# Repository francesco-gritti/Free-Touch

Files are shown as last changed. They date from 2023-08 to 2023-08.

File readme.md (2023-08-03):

# Free Touch

Water dispenser build for demonstration purpose without the device installed

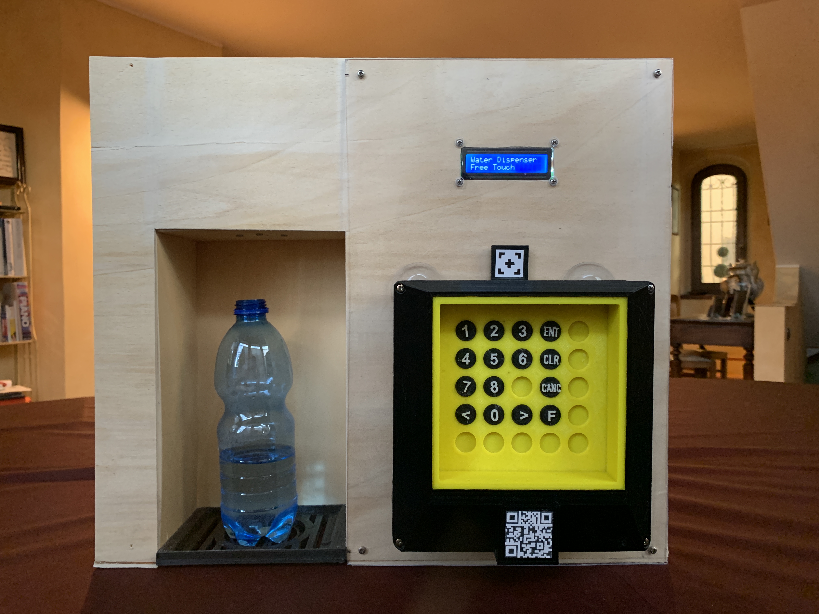
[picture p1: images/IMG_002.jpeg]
Water dispenser with the device installed


Free touch (which was tought during Covid 19) is a simple device that can be adapted to any keypad layout (like the ones of water dispenser machines, elevators and so on) and once mounted on top of it can press the buttons for you, avoiding you to have to touch anything. You can tell it the will to press a button by putting your finger closer to the target or by connecting with the smartphone via bluetooth

Free Touch can be adapted to the desired keypad layout just by taking a picture of it: an algorithm will recognize the buttons and calculate their position. Free Touch is then equipped with a tip that can move into the space and physically press buttons for you

Of course it would be easier to design products (water dispenser machines, elevators, ...) already equipped with bluetooth connectivity or non-touch user interaction, however there are so many machines that rely upon contact already that it would require an enormous effort to modifying them all

Okay this was me trying to make it look useful. It's not but conversely I think it's a nice little concentrate of engigneering: both electronics, mechanics and Informatics
Is that kind of device that solves a very simple problem in a very complicated way: wouldn't it be easier to design sime kind of stick you can hold in your hand and press the buttons with?
I still think that it was worth designing, building and programming it because it allowed me to enhance my knoledge of computer vision, 3d printing, mechanical design and embedded programming and was so much fun!

## Mobile App
For configuring the device (the process is explained in the next section) and for using it, I developed an application for smartphones using the Flutter framework so that it can be compiled for IOS and Android natively. The first version of the app used filtering, contrast enhancing and contour detection algorithm developed by me. In the second version I rightfully decided to integrate OpenCV which, of course, made the development much easier. Yet I think is a good way of proceeding: first develope something that work (doesn't have to be perfect) from scratch, then start using a library or a framework: first you learn from the ground up how something work and second but most important you can really appreciate those people that spend theire lives developing and then distributing theire work as open source. Many thanks to them!

Okay back to where I left...

## Configuration 
Before I mentioned that the device could be configured by taking a picture of it and can be controlled through bluetooth
Usually the configuration process confure people so I will try to explain how it works here:
- first of all you have to put a tag above the keypad you whish to configure (it will act as a reference to the algorithm to determine position and sizes)

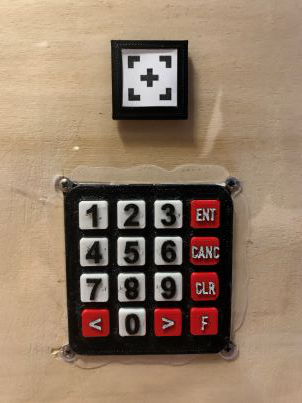
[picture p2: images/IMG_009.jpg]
Keyboard and tag

- than you open the application and connect to the device by scanning it's QR code

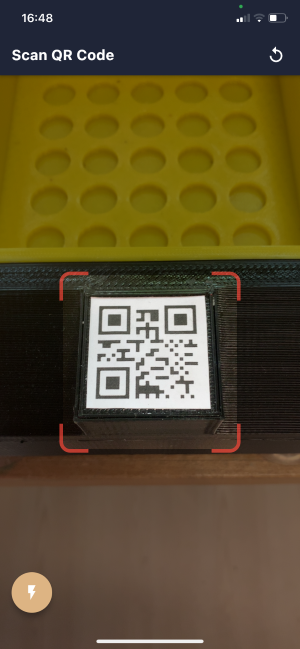
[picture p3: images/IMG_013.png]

- you take a picture of the keypad icluding the tag and the algorithm will automatically detect close edges that resembles pushbuttons



- Select the buttons you whish to configure

- Install the device aligning the slot on the top with the tag (this is necessary since the tag is the reference of the whole system and its position must be known)

Well Done! you can now press buttons at a distance, like magic!

this is the screen that appears when you connect to the device

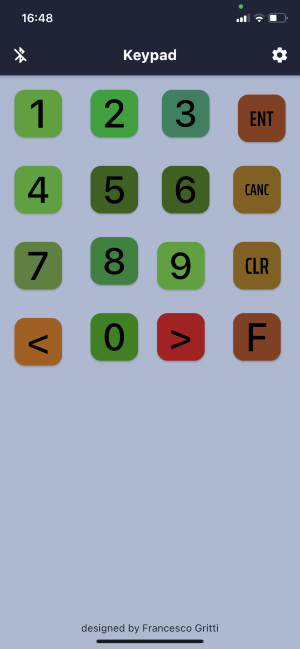
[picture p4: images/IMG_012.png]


## IR Sensor
on the front of the device there is a configurable matrix IR sensor matrix that allow the user to press the button by putting it's finger closer to it

The matrix is configurable in the meaning that behind each cell scanned by the IR sensors there is a slot where you can put an insert with written the actual button it corresponds to. This way the user can interact with it in a very natural way

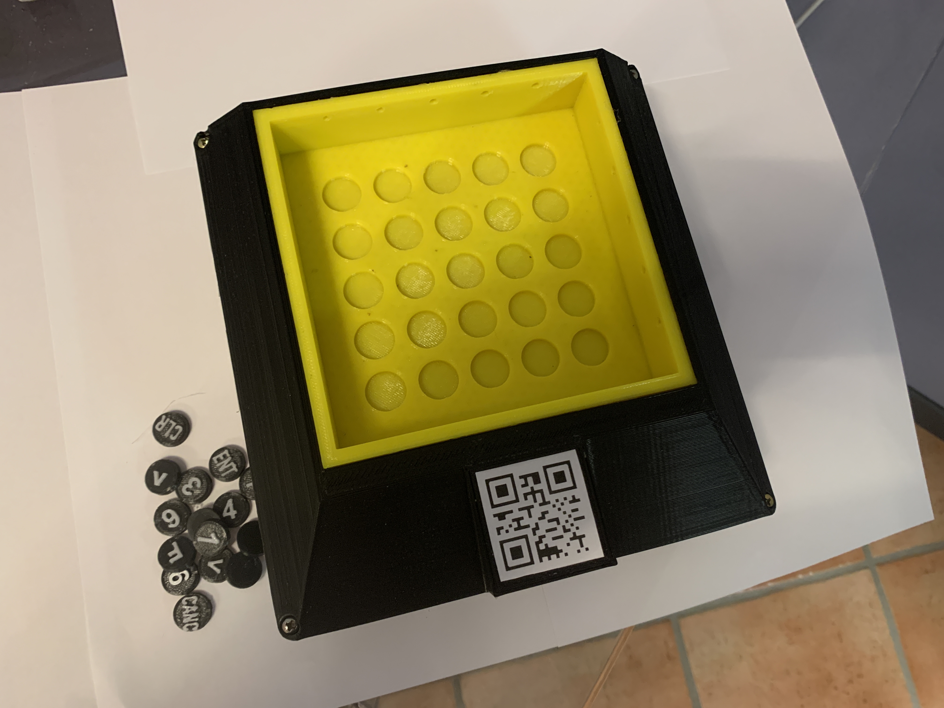
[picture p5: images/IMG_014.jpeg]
Before configuration


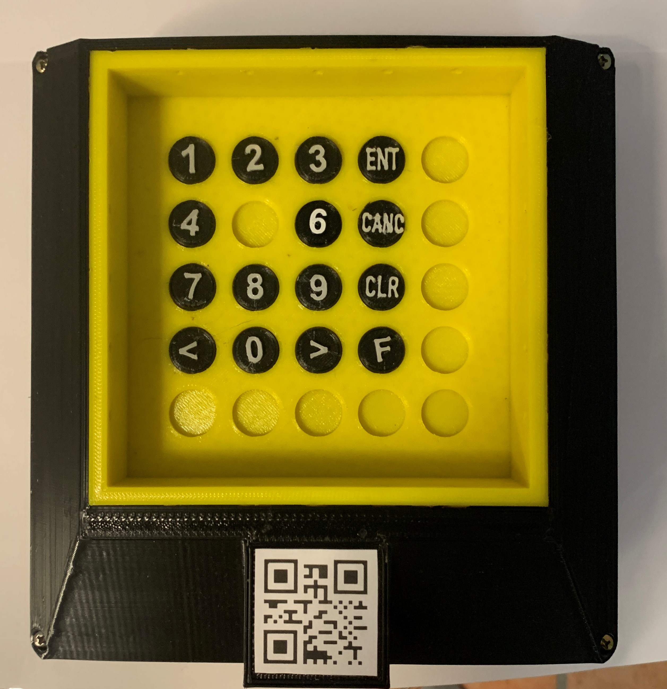
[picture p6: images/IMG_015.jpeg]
After configuration


## Mechanics

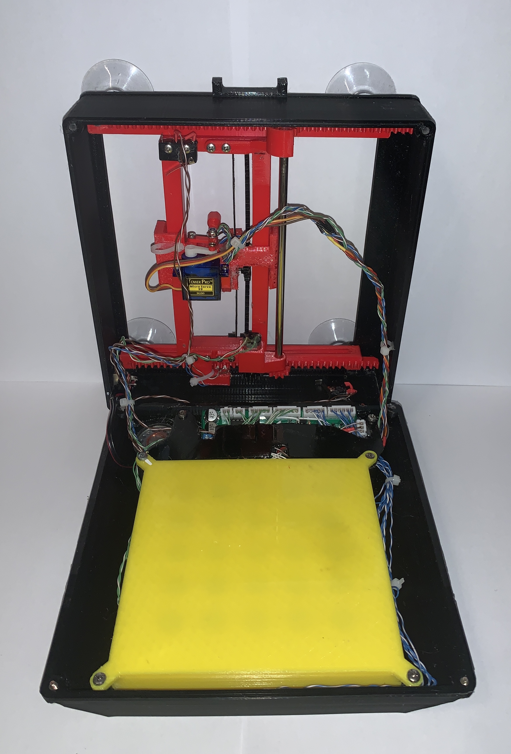
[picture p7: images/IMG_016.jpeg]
Internal of the device


All the mechanical parts are 3d printed using PETG. I decided to use this material since there are parts that slide on each other and PETG felt like a better material for this purpose in terms of friction with respect to PLA or ABS, and I didn't want to use PLA since it can easily deform even at not so high temperatures

I used little DC motors with reduction which turned out to be perfect for this application: small, light way yet they have good torque and speed

The axis position is monitored by optical encoder that were 3D printed int the structure itself

the buttons are effectively pressed by a sg90 servo motor

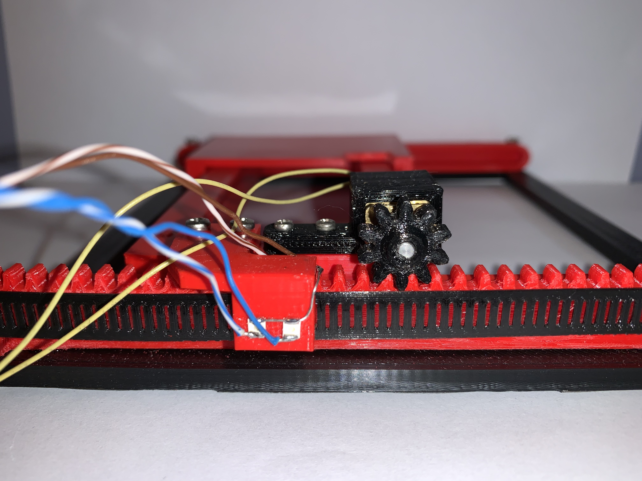
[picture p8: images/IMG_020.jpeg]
Details of the embedded encoder of one of the axis


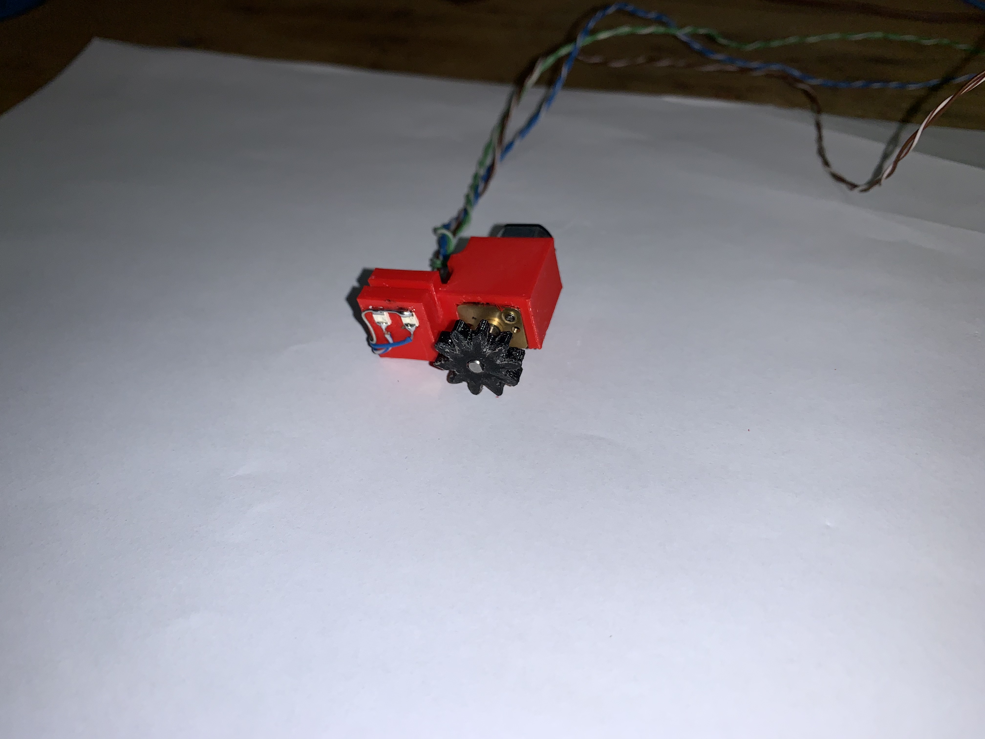
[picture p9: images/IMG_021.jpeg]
Details of oen of the motor assembly with embedded IR emitter and receiver to read position


## Electronics
And now the time for electronics

### Microcontroller
As for the microcontroller I have used the PIC16LF18456 which has a generous amount of peripherals, RAM and program memory, more than enough for this project

### Analog IR Signal Conditioning
IR sensor are driven at 1kHz so that the slow varying influence of light of the environment can be filtered out with active filters. no one wants a button to be pressed just because a cloud covered the sun for frew seconds!

### Bluetooth
The bluetooth connectivity is handled through Microchip's module ... communicating with the microcontroller via AT commands over UART

### PCB
I was a bit in a rush (as every time when you have a deadline to the project) and when designing the PCB I made some mistakes (that is why there should be always a version 2.0 of a PCB) but luckily that happens so frequently that even if it was two years ago I was already quite good at PCB rework
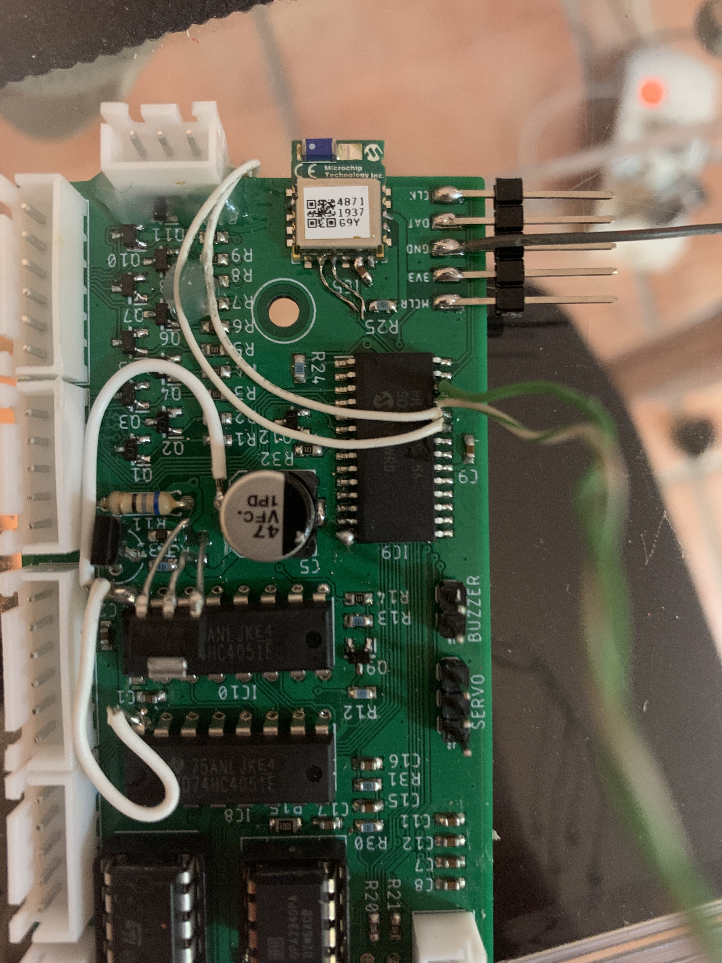
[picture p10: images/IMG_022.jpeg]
Issues here and there with the PCB design


## Cable management
I was almost forgetting (as I did while designing the device): cable management
In fact it's simple to overlook during design at cable management but it is most of the times critical. In this project everything had to fit in a tiny space and the axis had to move freely for almost the entire widtrh and length of the device. If even a tiny cable got stucked somewhere in the internal structure, the tip was blocked and many bad things can happen
Luckily after some trial and errors I managed to fix the cable in a very lovely way that was nicely organized and allowed the axis to move smoothly

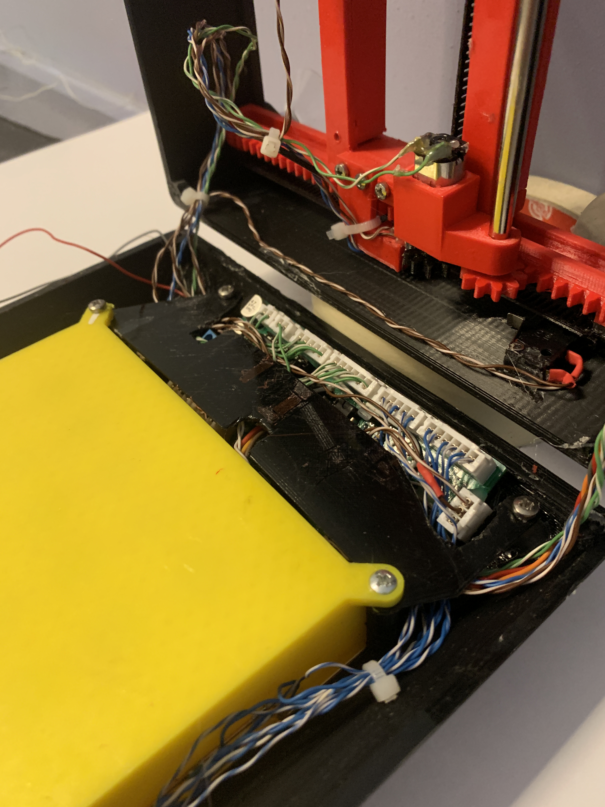
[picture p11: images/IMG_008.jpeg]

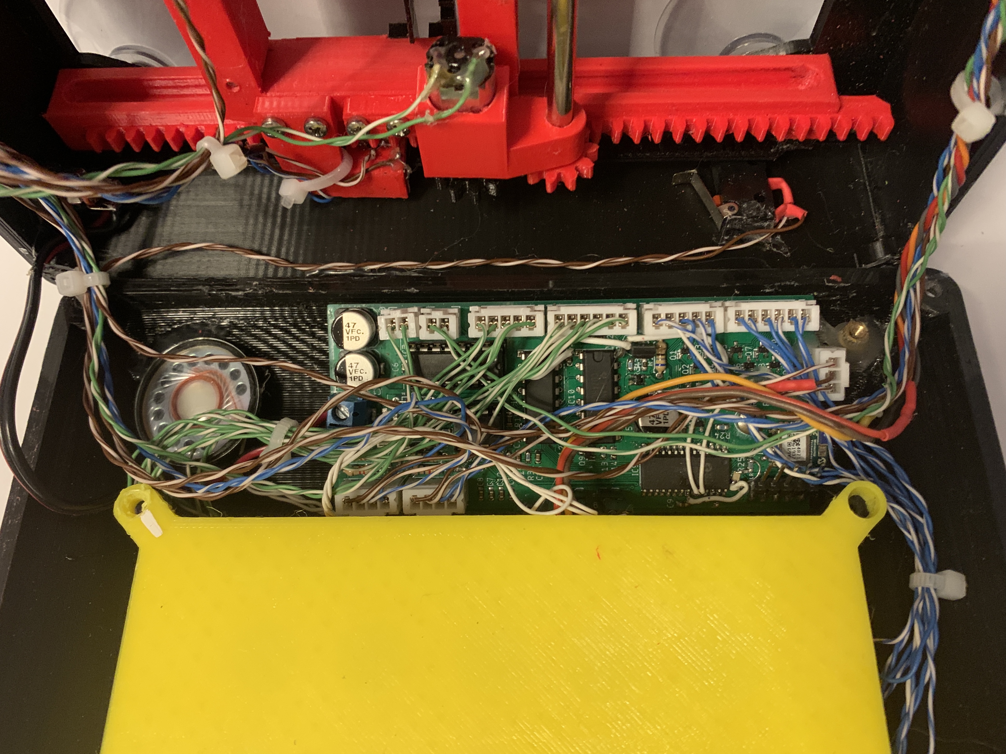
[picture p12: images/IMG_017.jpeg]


## Version 1.0

Well all I have been talking about and showing so far was version 2.0 of the device. Of course there have been a version 1.0 that was so ugly it almost feels a modern art creation
The concept is exactly the same, just messier. I will attach some pictures of it here 

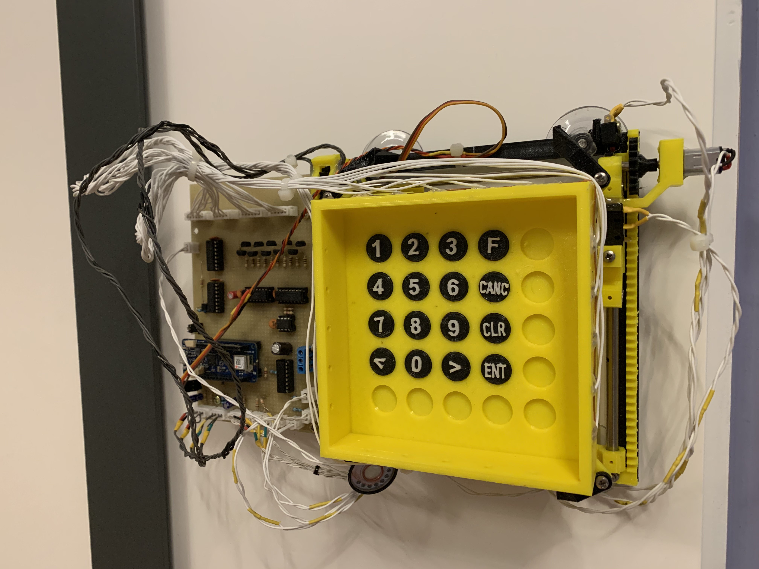
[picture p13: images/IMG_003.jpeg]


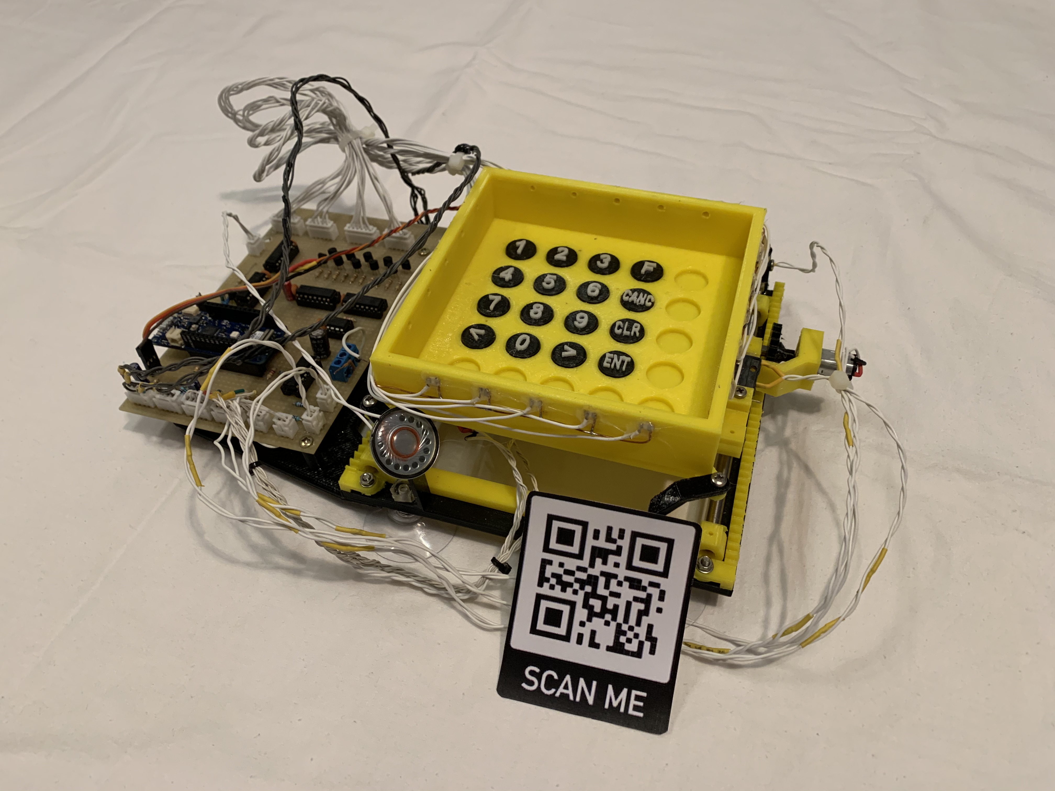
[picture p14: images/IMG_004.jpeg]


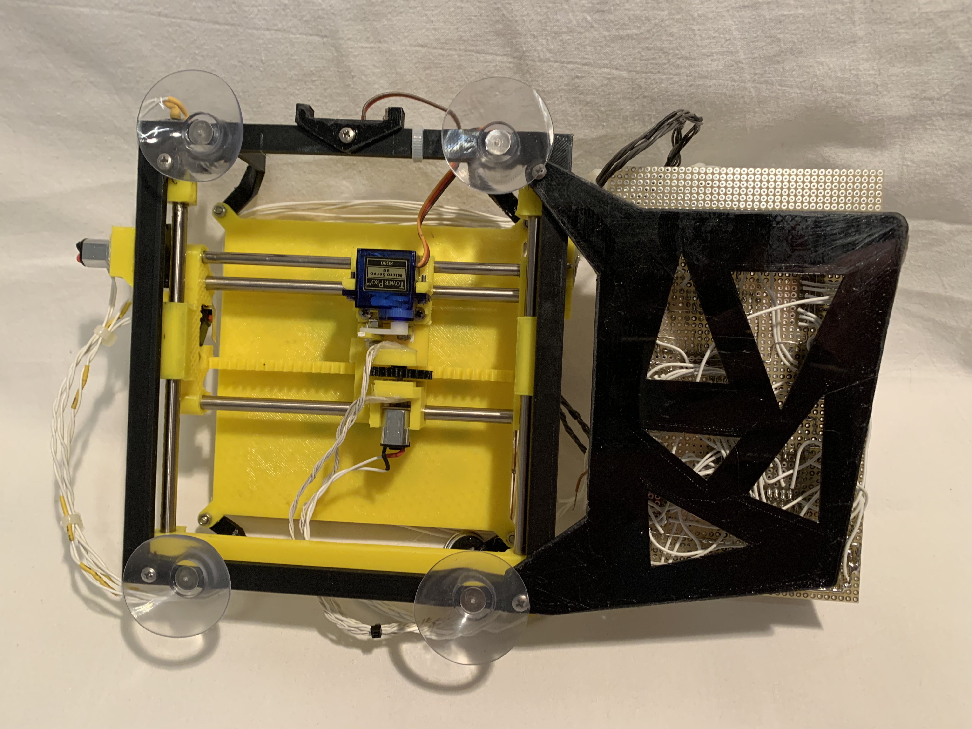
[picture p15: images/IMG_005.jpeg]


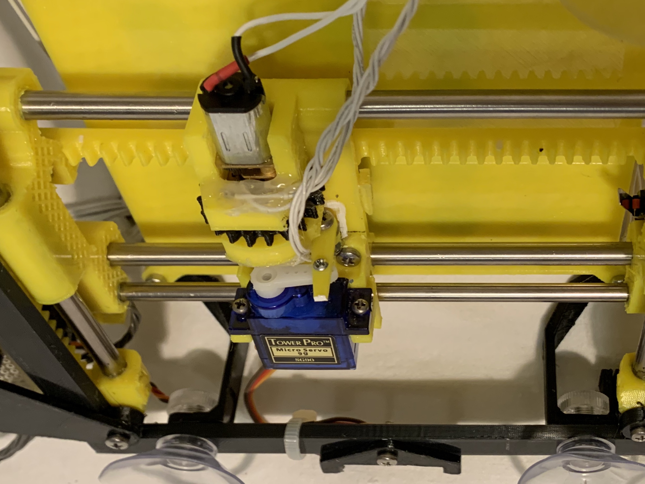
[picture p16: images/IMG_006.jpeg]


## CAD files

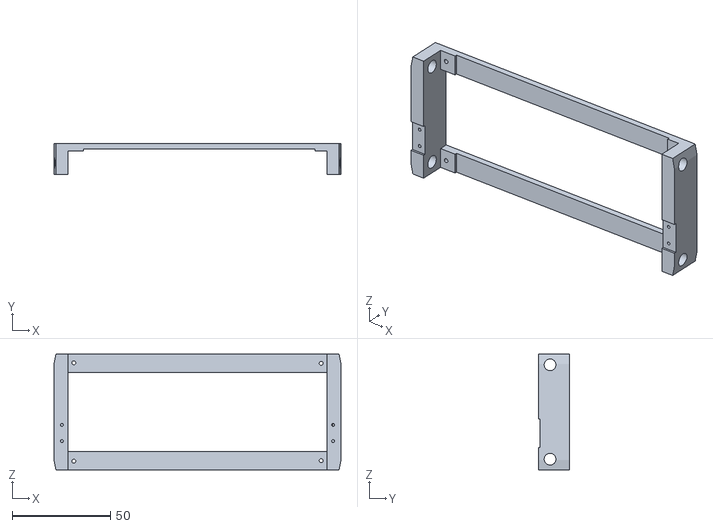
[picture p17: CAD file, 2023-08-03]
CAD/STL/Asse X/main_frame.stl
146.0 x 16.0 x 59.0

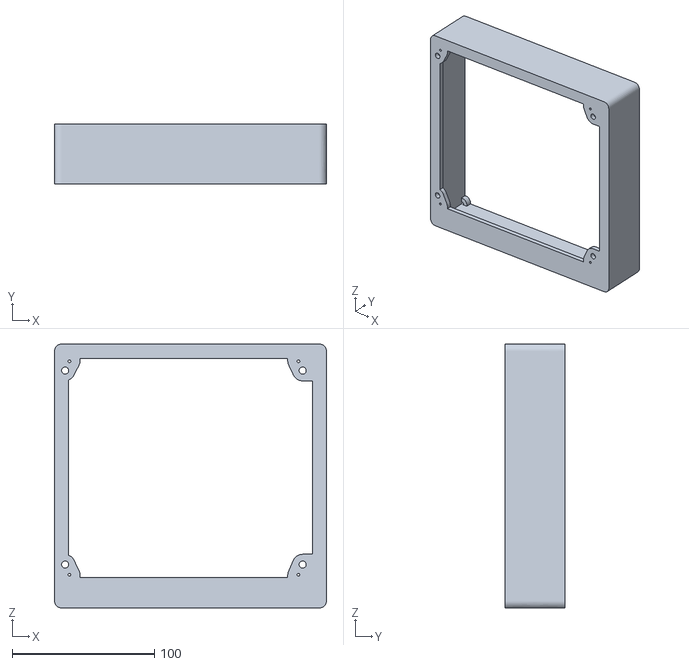
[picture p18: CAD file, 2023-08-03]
CAD/STL/keypad/enclosure_full.stl
191.2 x 42.0 x 185.5

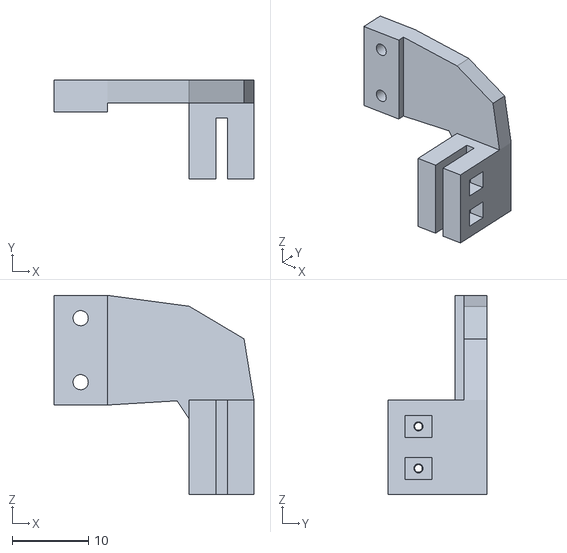
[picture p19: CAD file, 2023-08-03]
CAD/STL/Asse Y/enc_support.stl
26.2 x 13.0 x 26.2

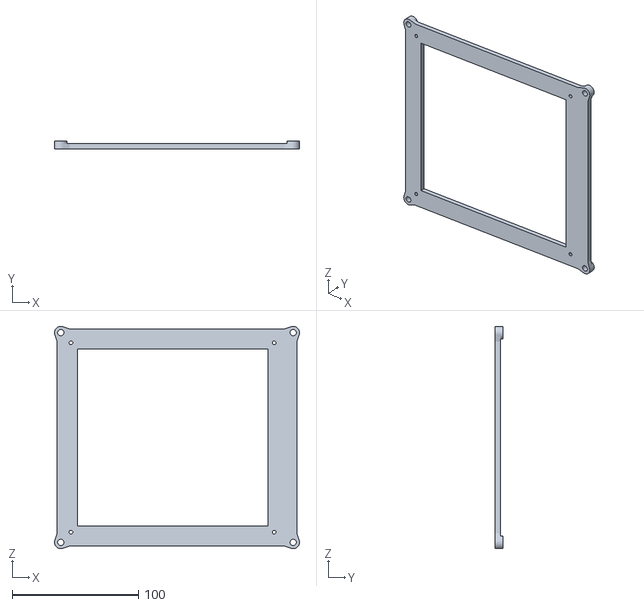
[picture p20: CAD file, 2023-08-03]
CAD/STL/base/base.stl
194.1 x 6.00 x 176.1

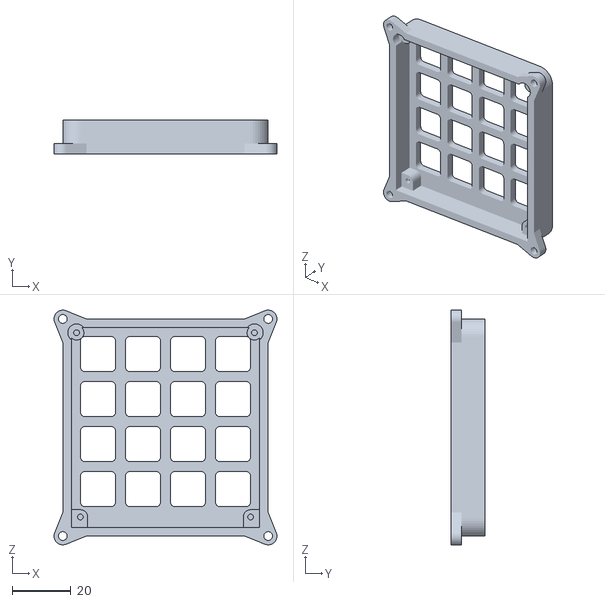
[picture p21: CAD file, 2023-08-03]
CAD/STL/keypad/keypad.stl
76.0 x 11.7 x 80.0

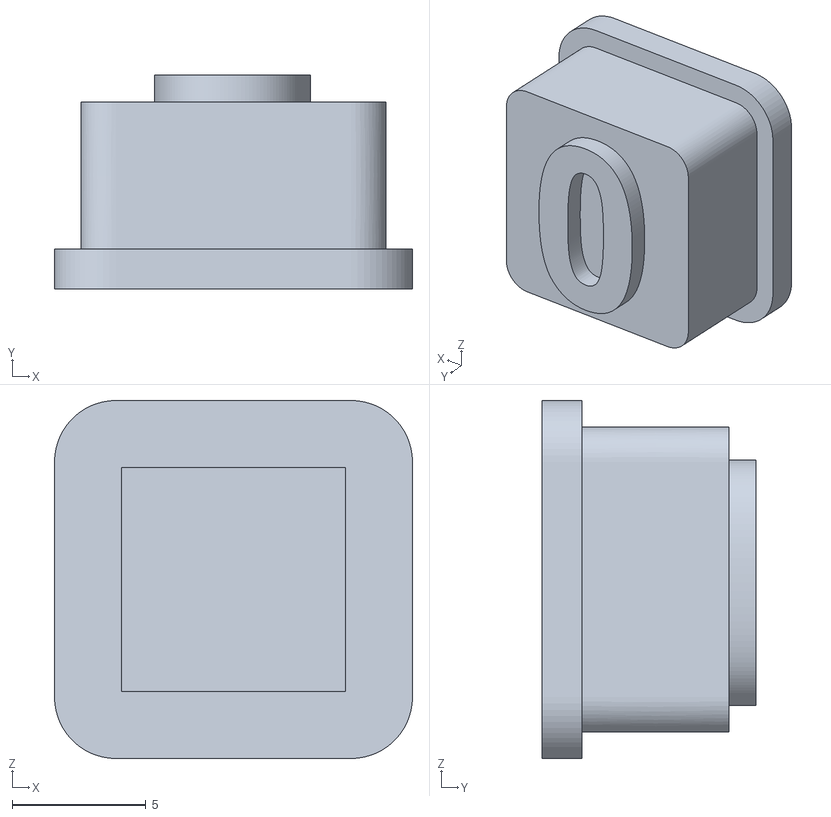
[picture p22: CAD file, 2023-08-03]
CAD/STL/keypad/keys/key0.stl
13.4 x 8.00 x 13.4

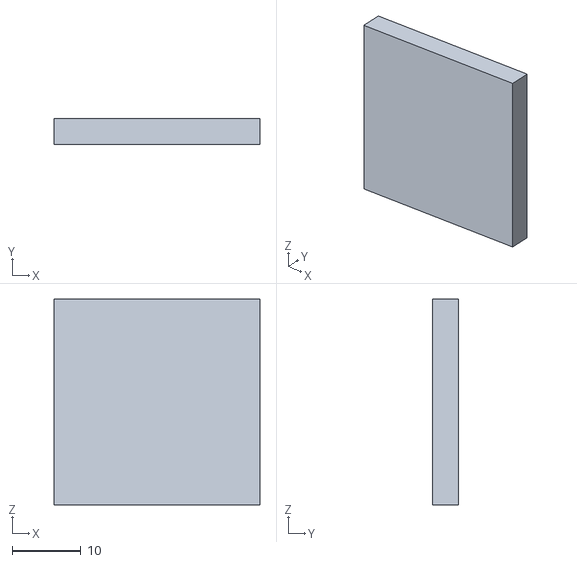
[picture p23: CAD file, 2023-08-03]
CAD/STL/tag_holder.stl
30.0 x 3.75 x 30.0

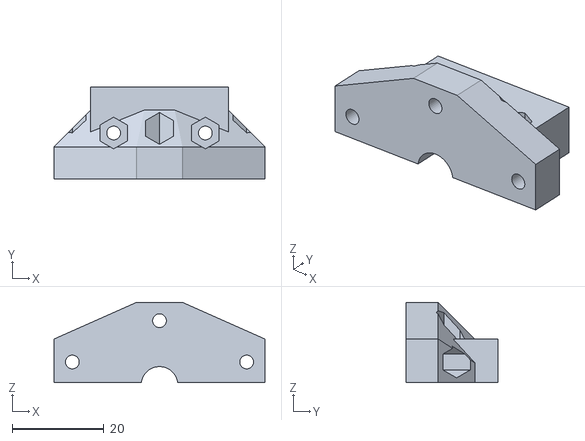
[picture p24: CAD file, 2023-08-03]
water dispenser/STL/Corpo1.stl
46.0 x 20.0 x 17.5

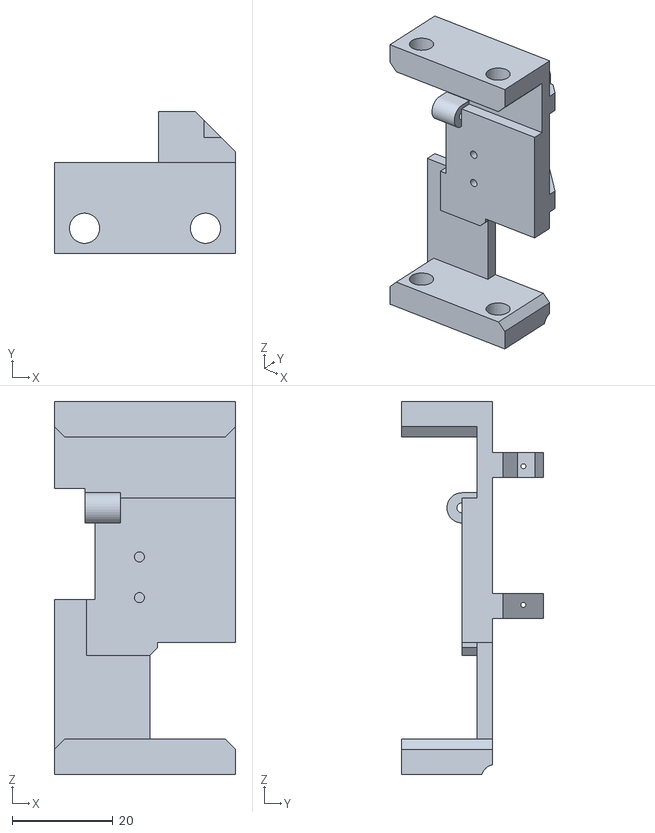
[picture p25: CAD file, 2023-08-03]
CAD/STL/Asse X/platform.stl
36.0 x 28.2 x 74.0

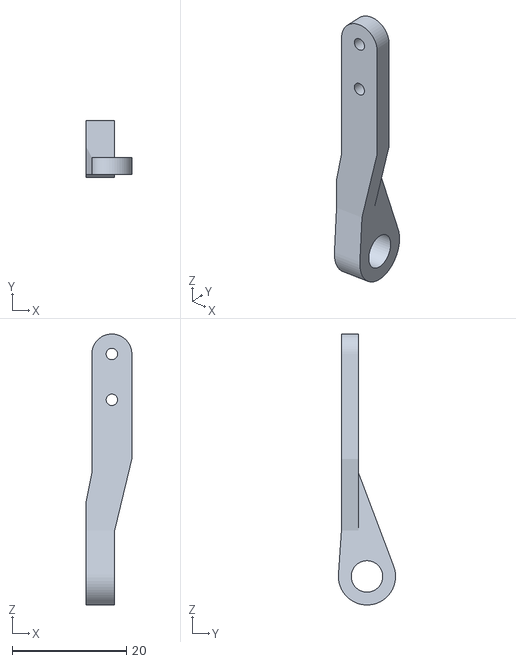
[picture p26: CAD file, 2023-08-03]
CAD/STL/Asse Y/supp1.stl
8.00 x 9.99 x 47.4

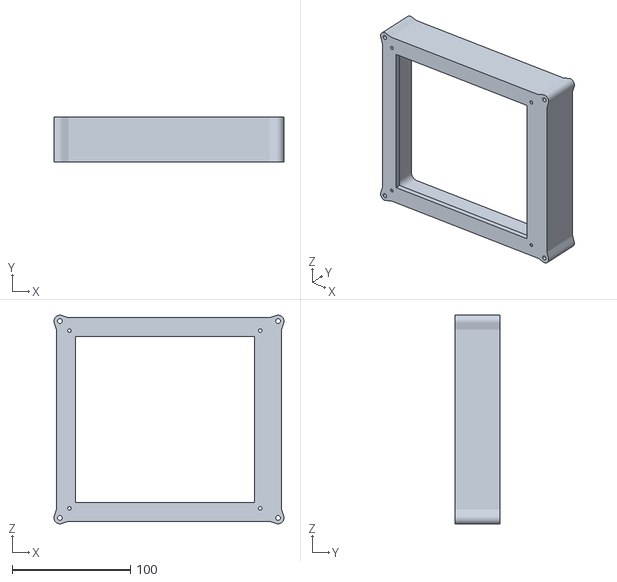
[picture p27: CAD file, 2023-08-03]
CAD/STL/base/enclosure.stl
194.1 x 38.0 x 176.1

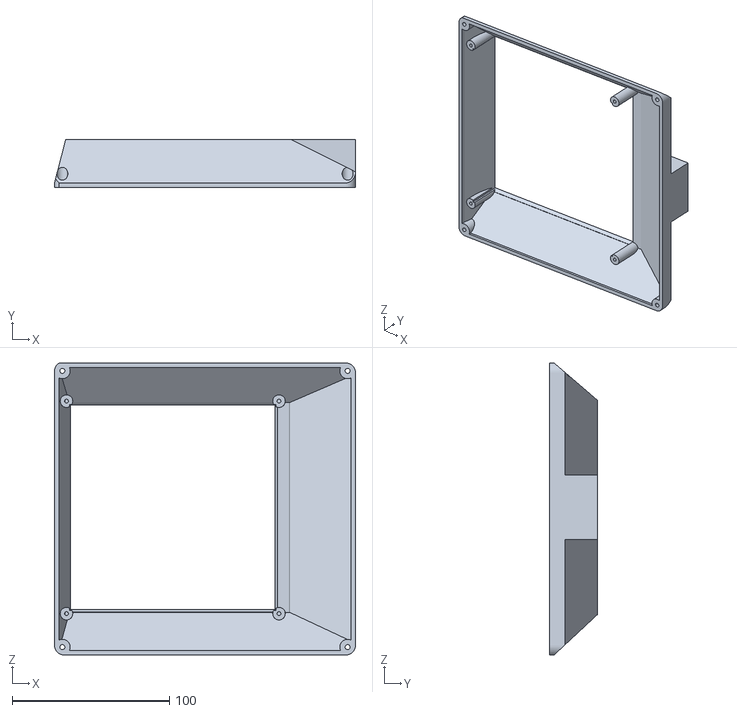
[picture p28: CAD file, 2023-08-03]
CAD/STL/keypad/enclosure_top.stl
191.2 x 30.6 x 185.5

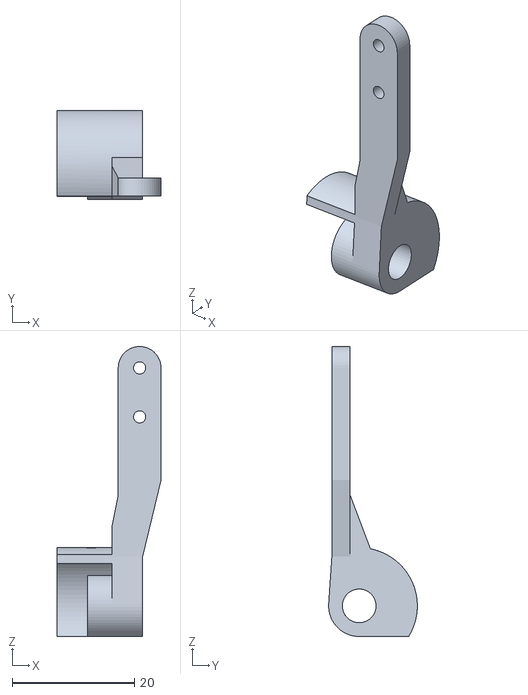
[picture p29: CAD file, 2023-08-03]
CAD/STL/s1.stl
17.0 x 14.5 x 47.4

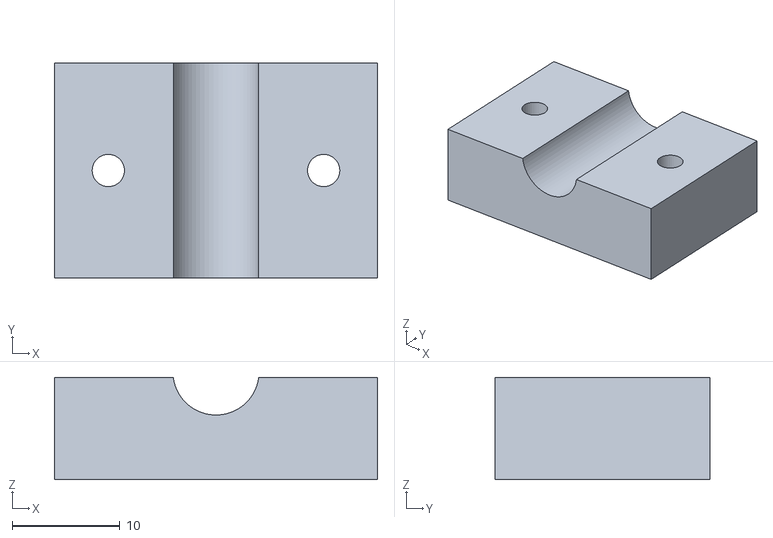
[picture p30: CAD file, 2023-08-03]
water dispenser/STL/Corpo2.stl
30.0 x 20.0 x 9.50

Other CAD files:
CAD/STL/keypad/keys/key5.stl
CAD/STL/Asse X/encoder_grid.stl
CAD/STL/Asse Y/guida.stl
CAD/STL/cable_squisher.stl
CAD/STL/Asse X/guide.stl
CAD/STL/Asse X/motor_encoder_support.stl
CAD/STL/Asse X/pin1.stl
CAD/STL/Asse X/rack.stl
CAD/STL/Asse X/tip1.stl
CAD/STL/Asse Y/Corpo1.stl
CAD/STL/Asse Y/encoder.stl
CAD/STL/Asse Y/gear.stl
CAD/STL/Asse Y/supp2.stl
CAD/STL/key_6.stl
CAD/STL/keypad/bottle_holder.stl
CAD/STL/keypad/key.stl
CAD/STL/keypad/keys/key1.stl
CAD/STL/keypad/keys/key2.stl
CAD/STL/keypad/keys/key3.stl
CAD/STL/keypad/keys/key4.stl
CAD/STL/keypad/keys/key6.stl
CAD/STL/keypad/keys/key7.stl
CAD/STL/keypad/keys/key8.stl
CAD/STL/keypad/keys/key9.stl
CAD/STL/keypad/keys/key_CANC.stl
CAD/STL/keypad/keys/key_CLR.stl
CAD/STL/keypad/keys/key_ENT.stl
CAD/STL/keypad/keys/key_F.stl
CAD/STL/keypad/keys/key.stl
CAD/STL/keypad/keys/key.stl
water dispenser/STL/pump_holder.stl

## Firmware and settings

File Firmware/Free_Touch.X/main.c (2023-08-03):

#include "main.h"



//#define DEBUG

// unique ID identifier of the device
const uint8_t manufacturerData[16] = "1234567890abcdef";


// GLOBAL VARIABLES
volatile int16_t posX, posY;
volatile int16_t targetX, targetY;
volatile int16_t posX_reached, posY_reached;

uint8_t matrix_enabled = 1;
int8_t prev_col = -1;
int8_t prev_row = -1;


uint8_t buttonToPress_buffer[5];
uint8_t btopress_idx = 0;
button_t buttonList [MAX_BUTTONS];
int8_t ID_grid [MAX_ROWS][MAX_COLS]; 
int buttonList_len;

bool toPress = false;


void pressButton (int buttonID);

uint8_t prev_connection_status = 0;

void main(void) {
    
    // initialize the device
    SYSTEM_Initialize();
    
    // keep RN4871 in a reset state
    BT_RST_SetHigh();
    
    // stop buzzer from playing
    TRISC |= 0b00001000;
    __delay_ms(2000);
    
    
    EUSART2_SetRxInterruptHandler(USART_Handler);
    IOCCF7_SetInterruptHandler (encoder1A_InterruptHandler);
    IOCCF6_SetInterruptHandler (encoder1B_InterruptHandler);
    IOCCF5_SetInterruptHandler (encoder2A_InterruptHandler);
    IOCCF4_SetInterruptHandler (encoder2B_InterruptHandler);
    
    TMR1_SetInterruptHandler (TMR1_ISRHandler);
    
    
    // load keypad configuration from EEPROM
    
    uint16_t addr = FIRST_EE_ADDR;
    uint8_t len = DATAEE_ReadByte (addr);
    if(len > 250) len = 250;
    addr += 1;
    for (uint8_t i=0;i<len; i+=1, addr += 1)
        payload[i] = DATAEE_ReadByte(addr);
    
    
    buttonList_len = createButtonList (payload, len, buttonList);
    arrangeButtonsInMatrix (buttonList, buttonList_len, ID_grid);

    
    
    // home the structure and set zero position. This
    // has to be done before interrupts are enables
#ifndef DEBUG
    homeMotorX();
    homeMotorY();
    __delay_ms(100);
    posX = 0;
    posY = 0;
    posX_reached = 1;
    posY_reached = 1;
#endif

   
    servoRelease();
    setAddress(0);
    
    INTERRUPT_GlobalInterruptEnable();
    INTERRUPT_PeripheralInterruptEnable();


    
    // ------------------------------------------//
    //            RN4871 COFNIGURATION           //
    // ------------------------------------------//
    
    reboot_flag = 0;
    BT_RST_SetLow();
    while(reboot_flag == 0);
    reboot_flag = 0;
    
    // enter command mode for configuration
    enterCommandMode ();
    while(cmd_flag == 0);
    cmd_flag = 0;
    
    // set  advertisement data
    setAdvertisementManufacturerData (manufacturerData, 16);
    while (aok_flag == 0);
    aok_flag = 0;
    
    setRandomAddress ();
    while(cmd_flag == 0);
    cmd_flag = 0;
    
    exitCommandMode();
    
    playTone(400);
    
    
    while (1)  {
        
        if(connection_status != prev_connection_status){
            
            prev_connection_status = connection_status;
            playTone(400);
        }
        
        
        // handle BT communication
        if (data_available) {
            
            data_available = 0;
            
            // write configuration into EEPROM memory
            if (payload[0] == SET_CONFIG_CMD) {
                // write data length
                uint16_t addr = FIRST_EE_ADDR;
                DATAEE_WriteByte (addr, data_len-1);
                // write data
                addr += 1;
                for (uint8_t i=1;i<data_len; i++, addr+=1)
                    DATAEE_WriteByte (addr, payload[i]);
                
                sendACK();
                
                
                buttonList_len = createButtonList (&payload[1], data_len-1, buttonList);
                arrangeButtonsInMatrix (buttonList, buttonList_len, ID_grid);
                
                // LOAD CONFIGURATION ()
            }

            
            // get configuration from EEPROM memory and send it
            else if (payload[0] == GET_CONFIG_CMD) {
                
                uint16_t addr = FIRST_EE_ADDR;
                uint8_t len = DATAEE_ReadByte (addr);
                if(len > 250) len = 250;
                
                
                // set payload start sequence
                payload [0] = 0x01;
                payload [1] = 0x02;
                payload [2] = 0x03;
                payload [3] = len+1;
                payload [4] = RESPONSE_TO_GET_CONFIG;
                
                addr += 1;
                for (uint8_t i=0;i<len; i+=1, addr += 1)
                    // set payload length and data content
                    payload[i+5] = DATAEE_ReadByte(addr);
                
                
                // send data in chunks of 150 Bytes. wait 10ms between a packet and the following
                uint8_t sent = 0;
                for (uint8_t i=0;i<len+5; i+=1, addr += 1) {
                    // send data
                    EUSART2_Write (payload[i]);
                    sent += 1;
                    if(sent >= 150) {
                        sent = 0;
                        __delay_ms(10);
                    }
                }
            }
            
            else if (payload[0] == PRESS_BUTTON_CMD) {
                
                playTone (200);
                
                int buttonID = payload[1];
                
                if (toPress == false)
                    pressButton(buttonID);
                
                else {
                    if(btopress_idx<5) {
                        
                        buttonToPress_buffer[btopress_idx++] = buttonID;
                    }
                }
            }
        }
        
        
        
     
        
        if(posX_reached && posY_reached && toPress){
            
            // press servo sequence
            servoPress();
            __delay_ms(300);
            servoRelease();
            
            toPress = 0;
            
            if (btopress_idx != 0) {
                
                pressButton (buttonToPress_buffer[0]);
                btopress_idx --;
                
                // move all IDS to the left
                for(int8_t i=1; i<=btopress_idx; i++)
                    buttonToPress_buffer[i-1] = buttonToPress_buffer[i];
            }
        }
   
        
        
        int8_t row = -1, col = -1;
        
        uint8_t i;
        for (i=0; i<5; i++){
            
            setAddress(i);
            __delay_ms(10);
            
            ADCC_StartConversion(channel_ANB0);
            while(!ADCC_IsConversionDone());
            uint16_t val = ADCC_GetConversionResult();
            
            if(val < IR_SENSOR_THRESHOLD){
                row = i;
                break;
            }
        }
        if(row != -1) {
            for (i = 5; i<10; i++){

                setAddress(i);
                __delay_ms(10);

                ADCC_StartConversion(channel_ANB0);
                while(!ADCC_IsConversionDone());
                uint16_t val = ADCC_GetConversionResult();
                if(val < IR_SENSOR_THRESHOLD){
                    col = i-5;
                    break;
                }
            }
            if(col != -1 && matrix_enabled) {
                
                matrix_enabled = 0;
                
                // if there is a button press running, add this ID to the stack.
                // otherwise go for pressing the button
                int buttonID = ID_grid[row][col];
                if (buttonID != -1) {
                    playTone (200);
                    if (toPress == false)
                        pressButton(buttonID);
                    
                    else {
                        if(btopress_idx < 5) {

                            buttonToPress_buffer[btopress_idx++] = buttonID;
                        }
                    }
                }
            }
        }
        
        if(row == -1 && col == -1){
            matrix_enabled = 1;
        }
    }
}



void playTone (int duration_ms) {
    
    
    double timerValue = 0xffff - (duration_ms * 15.5);
    TMR1_WriteTimer((uint16_t) timerValue);
    
    TRISC &= 0b11110111;
    TMR1_StartTimer();
}



void TMR1_ISRHandler (void) {
    
    TMR1_StopTimer();
    TRISC |= 0b00001000;
}





void pressButton (int buttonID) {
    
    int button_idx = getIdxForButtonWithID (buttonList, buttonID, buttonList_len);

    int targetPosX = 39 - buttonList[button_idx].xPos;
    int targetPosY = buttonList[button_idx].yPos - 49;

    setTargetX (targetPosX);
    setTargetY (targetPosY);

    toPress = true;
}   







// thrown by RC4
void encoder1A_InterruptHandler (void) {
    
    if (ENC1A_GetValue() == 1){
        if (ENC1B_GetValue() == 1) posX +=1;
        else posX -=1;
    }
    else {
        if (ENC1B_GetValue() == 1) posX -=1;
        else posX +=1;
    }
    
    
    if(posX > targetX+1){
        MOTOR1A_SetLow();
        MOTOR1B_SetHigh();
        posX_reached = 0;
    }
    else if(posX < targetX-1) {
        MOTOR1B_SetLow();
        MOTOR1A_SetHigh();
        posX_reached = 0;
    }
    else {
        MOTOR1A_SetLow();
        MOTOR1B_SetLow();
        posX_reached = 1;
    }
  
}

// thrown by RC5
void encoder1B_InterruptHandler (void){
    
   // if (ENC1A_GetValue() == 1) return;
    
    /*if (ENC1A_GetValue() == 1) posX ++;
    else posX --;*/
}

// thrown by RC6
void encoder2A_InterruptHandler (void){
    
    
    if(ENC2A_GetValue() == 1) {
        if (ENC2B_GetValue() == 1) posY ++;
        else posY --;
    }
    else {
        if (ENC2B_GetValue() == 1) posY --;
        else posY ++;
    }
    
    if(posY > targetY+1){
        MOTOR2A_SetLow();
        MOTOR2B_SetHigh();
        posY_reached = 0;
    }
    else if(posY < targetY-1) {
        MOTOR2B_SetLow();
        MOTOR2A_SetHigh();
        posY_reached = 0;
    }
    else {
        MOTOR2A_SetLow();
        MOTOR2B_SetLow();
        posY_reached = 1;
    }
}



// thrown by RC7
void encoder2B_InterruptHandler (void){
    
    /*if (ENC2A_GetValue() == 1) posY ++;
    else posY --;*/
}



inline void setAddress (uint8_t addr) {
     
    addr &= 0b00001111;
    LATA &= 0b11100001;
    LATA |= (addr << 1);
}

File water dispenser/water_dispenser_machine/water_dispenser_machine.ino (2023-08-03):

#include <LiquidCrystal_I2C.h>

LiquidCrystal_I2C lcd(0x27,16,2);  // set the LCD address to 0x27 for a 16 chars and 2 line display



#define pump_pin 12


uint8_t row_pin[4] = {7, 6, 5, 4};
uint8_t col_pin[4] = {8, 9, 10, 11};



const char values [4][4][5] =  {

  {{"1"}, {"2"}, {"3"}, {"ENT"}},
  {{"4"}, {"5"}, {"6"}, {"CANC"}},
  {{"7"}, {"8"}, {"9"}, {"CLR"}},
  {{"<"}, {"0"}, {">"}, {"F"}},
};



void setup() {


  for (uint8_t i = 0; i < 4; i++) {
    pinMode(row_pin[i], INPUT_PULLUP);
  }

  for (uint8_t i = 0; i < 4; i++) {
    pinMode(col_pin[i], INPUT_PULLUP);
  }


  Serial.begin(115200);
  Wire.setClock(400000);
 
  lcd.init();
  lcd.backlight();

  lcd.setCursor(0,0);
  lcd.print("Hai premuto:");

  pinMode(pump_pin, OUTPUT);
  digitalWrite(pump_pin, LOW);
}

void loop() {



  for (uint8_t i = 0; i < 4; i++) {

    pinMode(row_pin[i], OUTPUT);
    digitalWrite(row_pin[i], LOW);
    
    delay(1);


    for (uint8_t j = 0; j < 4; j++) {

      if (digitalRead(col_pin[j]) == LOW) {
        
        Serial.println(values[i][j]);
        lcd.setCursor(0,1);
        lcd.print(values[i][j]);
        lcd.print("   ");

        digitalWrite(pump_pin, HIGH);
        delay(2000);
       digitalWrite(pump_pin, LOW);
      }
      
    }

    pinMode(row_pin[i], INPUT_PULLUP);

    delay(1);

  }
}

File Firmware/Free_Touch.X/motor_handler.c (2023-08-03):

#include "motor_handler.h"
#include "mcc_generated_files/mcc.h"


extern int16_t targetX, posX, posX_reached;
extern int16_t targetY, posY, posY_reached;



void homeMotorX (void) {
    
    MOTOR1A_SetLow();
    MOTOR1B_SetHigh();
    while(BTN_X_GetValue() == 1);
    MOTOR1B_SetLow();
}

void setTargetX (int16_t _targetX) {
    
    if(_targetX < 0) _targetX = 0;
    if(_targetX > 88)_targetX = 88;
    targetX = _targetX;
    
    if(posX > _targetX+1){
        MOTOR1A_SetLow();
        MOTOR1B_SetHigh();
        posX_reached = 0;
    }
    else if(posX < _targetX-1) {
        MOTOR1B_SetLow();
        MOTOR1A_SetHigh();
        posX_reached = 0;
    }
    else {
        MOTOR1A_SetLow();
        MOTOR1B_SetLow();
        posX_reached = 1;
    }
}




void homeMotorY (void) {
    
    MOTOR2A_SetLow();
    MOTOR2B_SetHigh();
    while(BTN_Y_GetValue() == 1);
    MOTOR2B_SetLow();
}


void setTargetY (int16_t _targetY) {
    
    if(_targetY < 0) _targetY = 0;
    if(_targetY > 88)_targetY = 88;
    targetY = _targetY;
    
    if(posY > _targetY+1){
        MOTOR2A_SetLow();
        MOTOR2B_SetHigh();
        posY_reached = 0;
    }
    else if(posY < _targetY-1) {
        MOTOR2B_SetLow();
        MOTOR2A_SetHigh();
        posY_reached = 0;
    }
    else {
        MOTOR2A_SetLow();
        MOTOR2B_SetLow();
        posY_reached = 1;
    }
}
